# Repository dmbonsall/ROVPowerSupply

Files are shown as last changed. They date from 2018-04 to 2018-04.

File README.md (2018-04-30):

<h1>ROV Power Supply</h1>
<h2>A 1400W DC/DC converter for use with underwater Remotly Operated Vehicals (ROV)</h2>
<p>This power supply was designed to convert 48VDC to 12VDC and 5VDC for use in the MATE ROV competionion. It uses multiple DC/DC converters from Murata Power to perform the power conversions.</p>
<p>There are two versions of this power supply. The first supply is a simple version which only includes the converter modules and a handful of passives. The second version is a "smart" version which includes an arduino pro mini that interacts with the converter modules to monitor the state and power output of the 12V power modules.</p>
<p>Unfortunatly our team lost funding before this could be manufactured, however the hardware design is complete and has been successfully passed a design/electrical rule check provided by Texas A&M University. A BOM for each version is provided with manufacturer and vendor part numbers.</p>

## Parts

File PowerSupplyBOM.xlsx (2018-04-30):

Part No. | Manufacturer Part No. | Vendor | Vendor Part No. | Price | Qty | Description | Totals
U1, U2 | DRQ-12/50-L48NKSA-C | Digikey | 811-3046-ND | $100.15 | 2 | 12VDC Converter | $200.30
U3 | ULS-5/20-D48N-C | Digikey | 811-2789-ND | $36.72 | 1 | 5VDC Converter | $36.72
U4 | Arduino Pro Mini 5V | Sparkfun | DEV-11113 | $9.99 | 1 | Microcontroller Breakout | $9.99
U5 | LM321MF/NOPB | Digikey | LM321MF/NOPBCT-ND | $0.67 | 1 | Op amp | $0.67
R1, R2 | RC0603FR-074K7L | Digikey | 311-4.70KHRCT-ND | $0.10 | 2 | 4.7kohm resitor | $0.20
R3 - R5 | RC0603FR-07150RL | Digikey | 311-150HRCT-ND | $0.10 | 3 | 150ohm Resistor | $0.30
R6 - R7 | RC0603FR-0710KL | Digikey | 311-10.0KHRCT-ND | $0.10 | 2 | 10kohm Resistor | $0.20
R8 - R10 | RC0603FR-0733KL | Digikey | 311-33.0KHRCT-ND | $0.10 | 3 | 33kohm Resistor | $0.30
R11 | RC0603FR-0747KL | Digikey | 311-47.0KHRCT-ND | $0.10 | 1 | 47kohm Resistor | $0.10
D1 - D3 | 150120RS75000 | Digikey | 732-4991-1-ND | $0.34 | 3 | LED, Red | $1.02
C1 | EEV-FK1K101Q | Digikey | PCE3493CT-ND | $1.28 | 1 | 100u Cap | $1.28
C2 | EEE-FK1K100XP | Digikey | PCE3827CT-ND | $0.60 | 1 | 10u Cap | $0.60
C3, C4 | CC0603KRX7R0BB102 | Digikey | 311-1467-1-ND | $0.10 | 2 | 1u Cap | $0.20
J3 - J4 | 1777600 | Digikey | 277-9763-ND | $7.95 | 2 | 12V Terminals | $15.90
J5 - J6 | 1751264 | Digikey | 277-5744-ND | $2.28 | 2 | 5V Terminals | $4.56
n/a | Break Away Headers | Sparkfun | PRT-00116 | $1.50 | 4 | Headers | $6.00
 |  |  |  |  |  |  | $278.34

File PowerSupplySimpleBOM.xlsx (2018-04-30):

Part No. | Manufacturer Part No. | Vendor | Vendor Part No. | Price | Qty | Description | Totals
U1, U2 | DRQ-12/50-L48NKS-C | Digikey | 811-3046-ND | $93.05 | 2 | 12VDC Converter | $186.10
U3 | ULS-5/20-D48N-C | Digikey | 811-2789-ND | $36.72 | 1 | 5VDC Converter | $36.72
C1 | EEV-FK1K101Q | Digikey | PCE3493CT-ND | $1.28 | 1 | 100u Cap | $1.28
C2 | EEE-FK1K100XP | Digikey | PCE3827CT-ND | $0.60 | 1 | 10u Cap | $0.60
C3 | CC0603KRX7R0BB102 | Digikey | 311-1467-1-ND | $0.10 | 1 | 1u Cap | $0.10
J3 - J4 | 1777600 | Digikey | 277-9763-ND | $7.95 | 2 | 12V Terminals | $15.90
J5 - J6 | 1751264 | Digikey | 277-5744-ND | $2.28 | 2 | 5V Terminals | $4.56
 |  |  |  |  |  |  | $245.26

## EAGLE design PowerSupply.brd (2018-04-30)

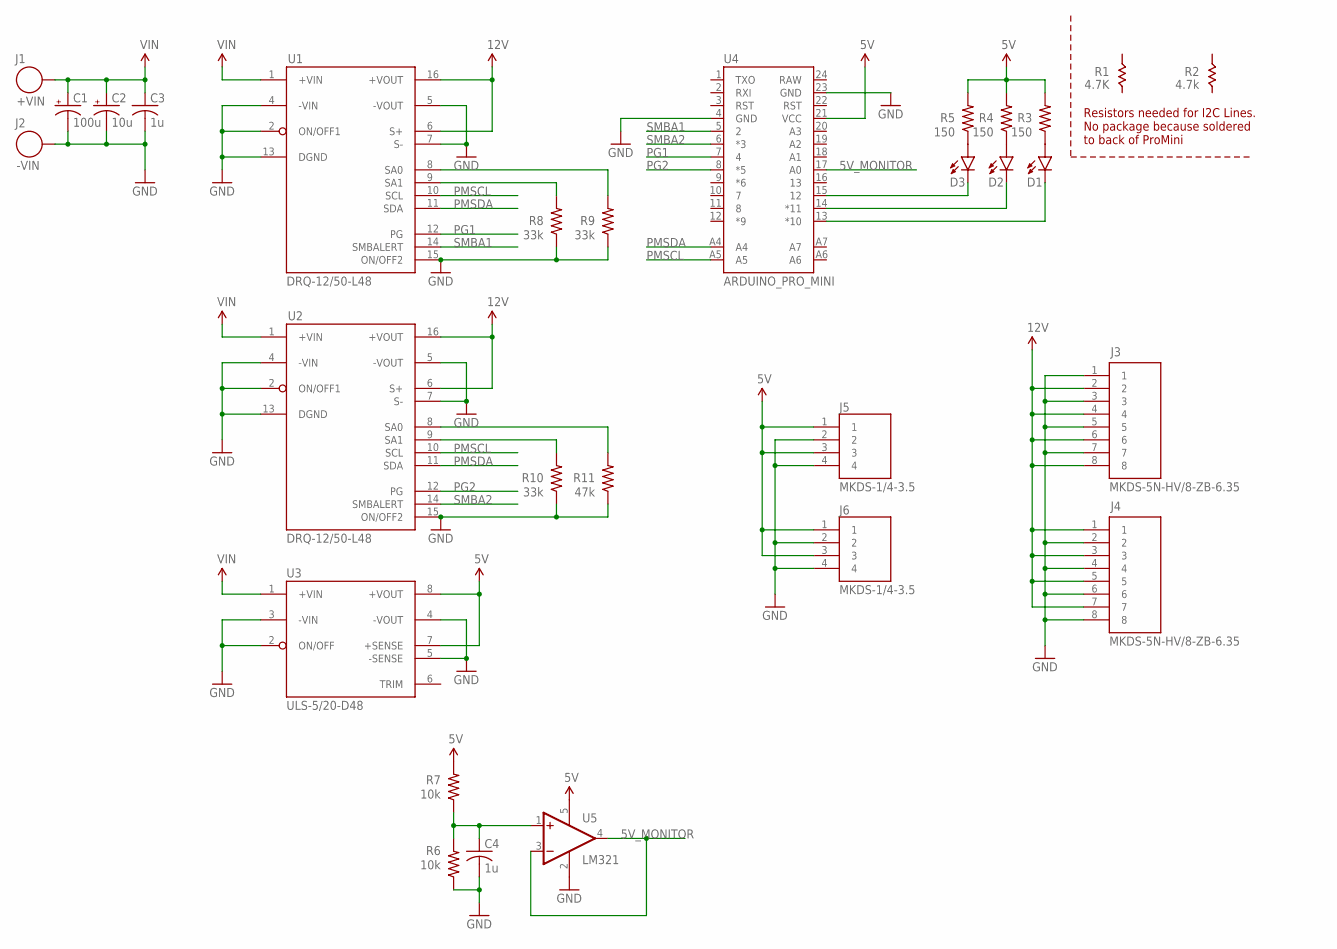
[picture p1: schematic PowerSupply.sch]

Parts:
C1: 100u; PANASONIC_E
C2: 10u; PANASONIC_D
C3, C4: 1u; C0603
D1, D2, D3: LED1206; LED-1206
J1: +VIN; 10AWG
J2: -VIN; 10AWG
J3, J4: MKDS-5N-HV/8-ZB-6.35; 1777600
J5, J6: MKDS-1/4-3.5; 1751264
R3, R4, R5: 150; 0603-RES
R6, R7: 10k; 0603-RES
R8, R9, R10: 33k; 0603-RES
R11: 47k; 0603-RES
U1, U2: DRQ-12/50-L48; ABC(PMBUS)
U3: ULS-5/20-D48; 1/16_BRICK_THROUGH_HOLE
U4: ARDUINO_PRO_MINI
U5: LM321; SOT23-5

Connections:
5V: J5.1, J5.3, J6.1, J6.3, R3.2, R4.2, R5.2, R7.2, U3.7 (+SENSE), U3.8 (+VOUT), U4.21 (VCC), U5.5 (V+)
5V_MONITOR: U4.17 (A0), U5.3 (-IN), U5.4 (OUT)
12V: J3.2, J3.4, J3.6, J3.8, J4.1, J4.3, J4.5, J4.7, U1.6 (S+), U1.16 (+VOUT), U2.6 (S+), U2.16 (+VOUT)
GND: C1.-, C2.-, C3.2, C4.2, J2.P$1, J3.1, J3.3, J3.5, J3.7, J4.2, J4.4, J4.6, J4.8, J5.2, J5.4, J6.2, J6.4, R6.1, R8.1, R9.1, R10.1, R11.1, U1.2 (ON/OFF1), U1.4 (-VIN), U1.5 (-VOUT), U1.7 (S-), U1.13 (DGND), U1.15 (ON/OFF2), U2.2 (ON/OFF1), U2.4 (-VIN), U2.5 (-VOUT), U2.7 (S-), U2.13 (DGND), U2.15 (ON/OFF2), U3.2 (ON/OFF), U3.3 (-VIN), U3.4 (-VOUT), U3.5 (-SENSE), U4.4 (GND), U4.23 (GND), U5.2 (V-)
unnamed: R10.2, U2.9 (SA1)
unnamed: C4.1, R6.2, R7.1, U5.1 (+IN)
unnamed: R11.2, U2.8 (SA0)
unnamed: R8.2, U1.9 (SA1)
unnamed: R9.2, U1.8 (SA0)
unnamed: D3.C, U4.15 (12)
unnamed: D2.C, U4.14 (*11)
unnamed: D1.C, U4.13 (*10)
unnamed: D1.A, R3.1
unnamed: D2.A, R4.1
unnamed: D3.A, R5.1
PG1: U1.12 (PG), U4.7 (4)
PG2: U2.12 (PG), U4.8 (*5)
PMSCL: U1.10 (SCL), U2.10 (SCL), U4.A5
PMSDA: U1.11 (SDA), U2.11 (SDA), U4.A4
SMBA1: U1.14 (SMBALERT), U4.5 (2)
SMBA2: U2.14 (SMBALERT), U4.6 (*3)
VIN: C1.+, C2.+, C3.1, J1.P$1, U1.1 (+VIN), U2.1 (+VIN), U3.1 (+VIN)

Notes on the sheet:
Resistors needed for I2C Lines. No package because soldered to back of ProMini

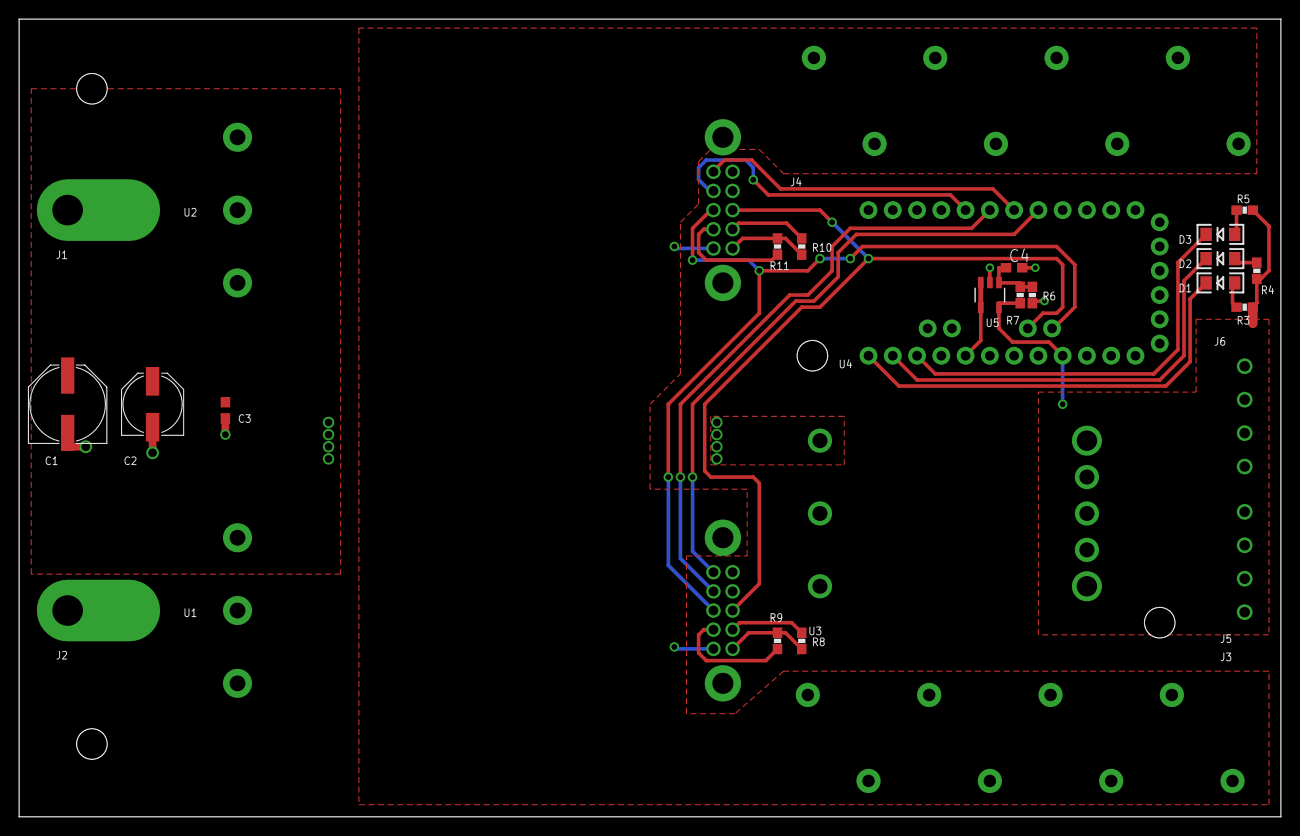
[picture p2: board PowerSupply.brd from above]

Board: 2 copper layers, 132.1 x 83.5 mm, 27 parts (0 on the bottom side), 22 nets.

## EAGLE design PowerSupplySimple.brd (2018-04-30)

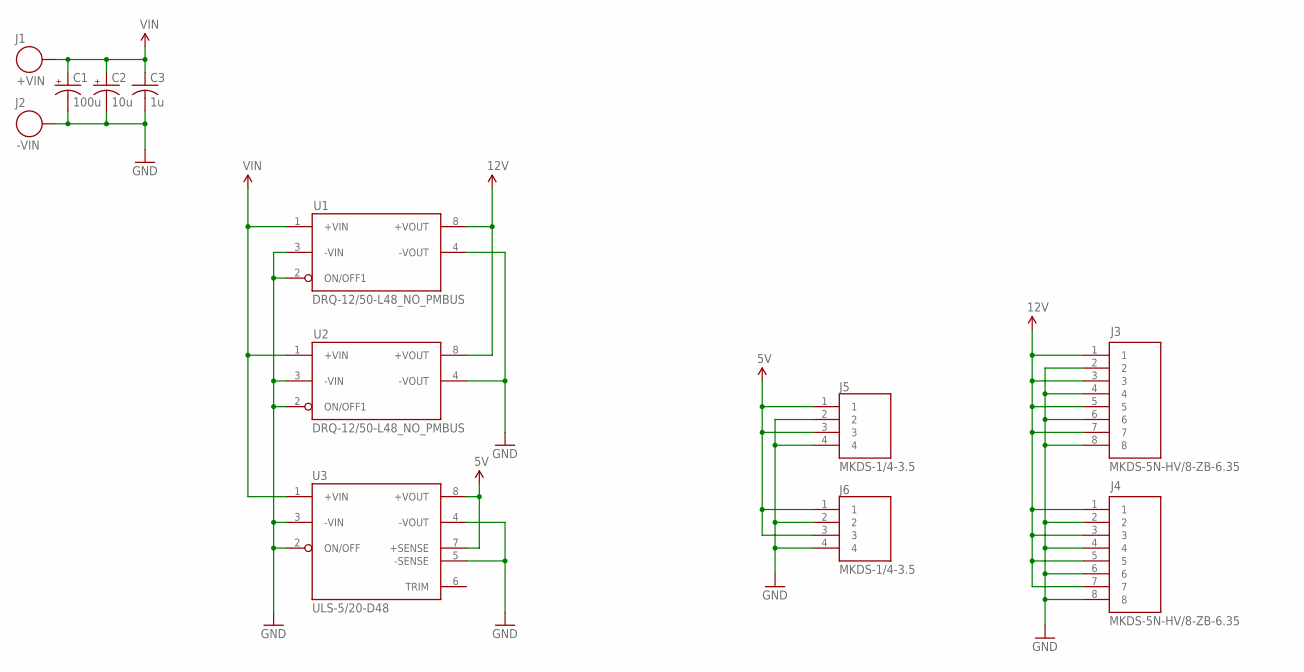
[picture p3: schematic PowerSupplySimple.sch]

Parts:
C1: 100u; PANASONIC_E
C2: 10u; PANASONIC_E
C3: 1u; C0603
J1: +VIN; 10AWG
J2: -VIN; 10AWG
J3, J4: MKDS-5N-HV/8-ZB-6.35; 1777600
J5, J6: MKDS-1/4-3.5; 1751264
U1, U2: DRQ-12/50-L48_NO_PMBUS; DRQ(NO_PMBUS)
U3: ULS-5/20-D48; 1/16_BRICK_THROUGH_HOLE

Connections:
5V: J5.1, J5.3, J6.1, J6.3, U3.7 (+SENSE), U3.8 (+VOUT)
12V: J3.1, J3.3, J3.5, J3.7, J4.1, J4.3, J4.5, J4.7, U1.8 (+VOUT), U2.8 (+VOUT)
GND: C1.-, C2.-, C3.2, J2.P$1, J3.2, J3.4, J3.6, J3.8, J4.2, J4.4, J4.6, J4.8, J5.2, J5.4, J6.2, J6.4, U1.2 (ON/OFF1), U1.3 (-VIN), U1.4 (-VOUT), U2.2 (ON/OFF1), U2.3 (-VIN), U2.4 (-VOUT), U3.2 (ON/OFF), U3.3 (-VIN), U3.4 (-VOUT), U3.5 (-SENSE)
VIN: C1.+, C2.+, C3.1, J1.P$1, U1.1 (+VIN), U2.1 (+VIN), U3.1 (+VIN)

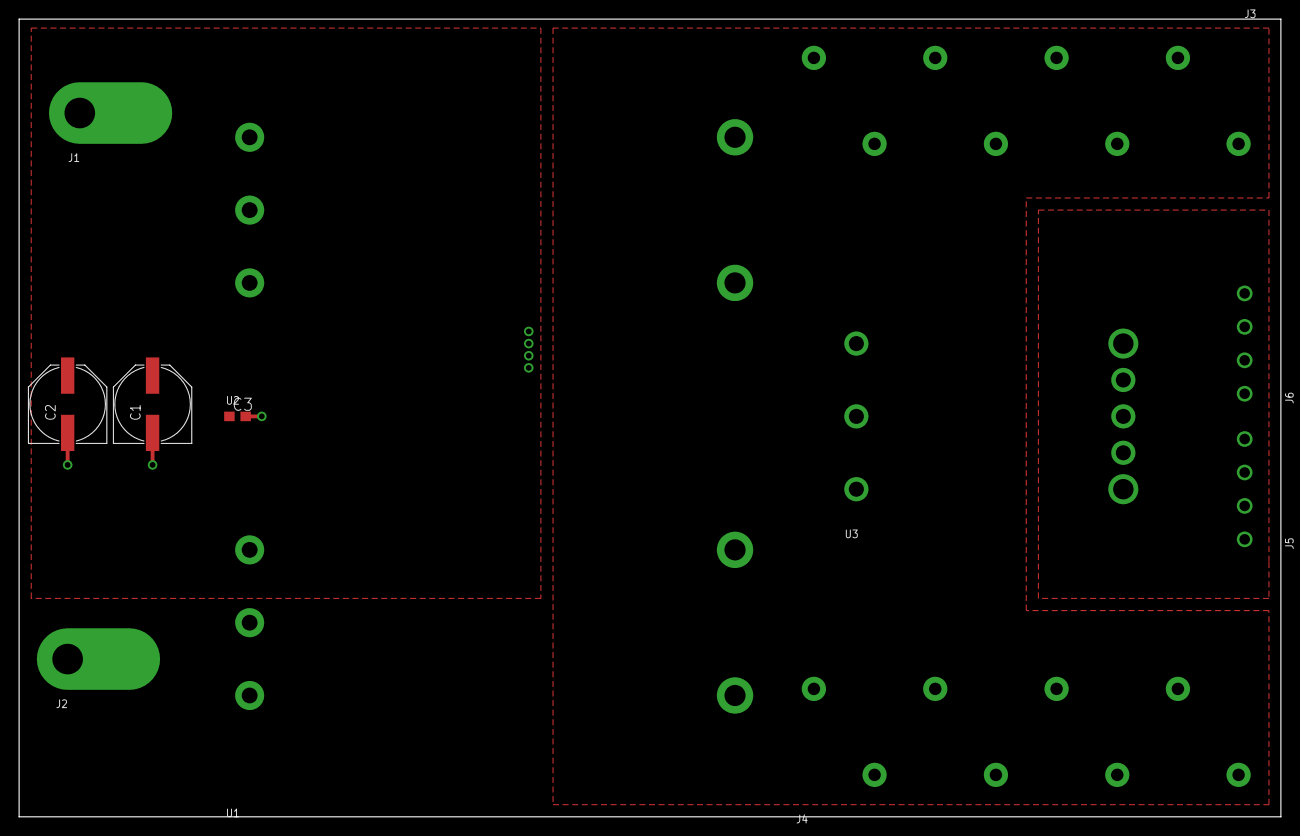
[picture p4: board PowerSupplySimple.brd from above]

Board: 2 copper layers, 132.1 x 83.5 mm, 12 parts (0 on the bottom side), 4 nets.

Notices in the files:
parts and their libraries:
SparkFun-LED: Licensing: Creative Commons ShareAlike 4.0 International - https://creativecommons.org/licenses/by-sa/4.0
